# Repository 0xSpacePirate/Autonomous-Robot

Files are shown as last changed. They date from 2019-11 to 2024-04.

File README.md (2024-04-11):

## Self-balancing-Robot

This project focuses on building an autonomous single-wheeled self-balancing
humanoid robot made from scratch. This report presents the techniques used to
design the robot and using reinforcement learning (RL) and a PID Controller make it
self-balancing. In the project was also included a 3D Simulation.

One of the goals of the project was to make a brand new robot design and not copy
from the already created ones on the internet. The design was supposed to represent
the Robert Gordon University robot (see image below):

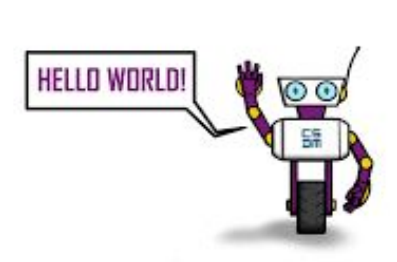
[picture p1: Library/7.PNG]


## Please refer to the pdf document for more detailed information! 
The pdf document can be found at: [Honours Project Report](https://github.com/SpacePirato/Autonomous-Robot/blob/master/Library/Honours%20Report%20-%20PETAR%20BONCHEV%20(1607262).pdf)

More info on the motivation & literature review can be found in the PDF document - chapters: 1-2;

-----------------------------------------------------------------------------------

The hardware that was used to control the robot:
1. Raspberry Pi 4 Model B
2. Gyroscope MPU-6050
3. Servo DXW90 (plastic) & Servo MG90S (metal) - both modified in 
                      order to be able to rotate with 360 degrees
4. Jumper cables
5. 6 AA 2900mAh batteries
6. Battery holder
7. UBEC 5V switch regulator

The first prototype can be seen below:

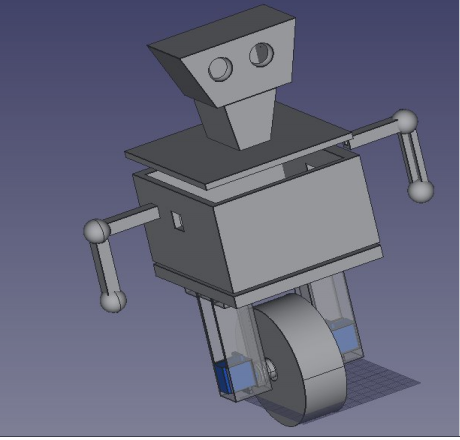
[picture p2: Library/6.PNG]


More info on the setup can be found in the PDF document - chapter: 3;

-----------------------------------------------------------------------------------

The design of the second prototype is more sophisticated and showed better results, 
however the legs had to be extended due to the reason that the robot was falling to quickly.

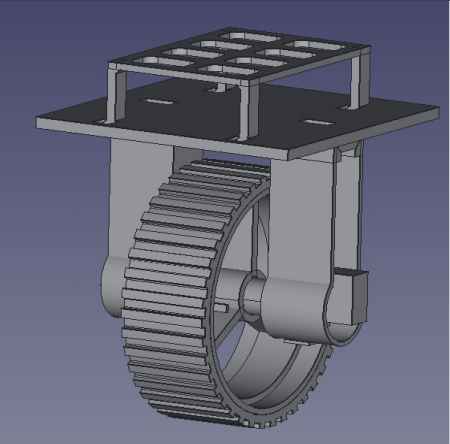
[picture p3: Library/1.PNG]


**The project was not finished**. Partially working self balacing robot using only a PID controller.
Examples can be seen below which represent the results from the first prototype:

-----------------------------------------------------------------------------------

The results from the two prototypes show that with the many improvements implemented, 
the robot manages to self balance itself better and better but not fully.

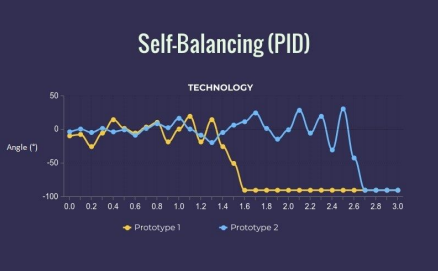
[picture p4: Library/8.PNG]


More detailed info on the results can be found in the PDF document - chapter 8;

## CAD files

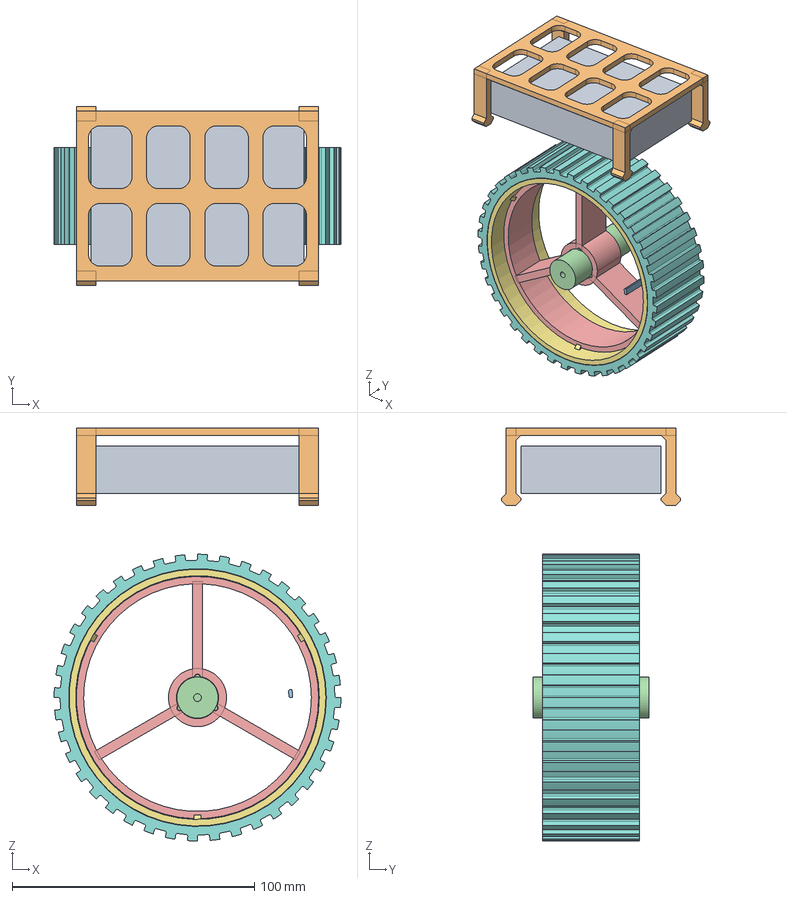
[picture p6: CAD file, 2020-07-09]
RobotAutoCAD/SecondPrototypeFinal.FCStd
118.4 x 74.0 x 170.5 mm
RPi
battery platform001
thread cut rounded for bigger tyre
axis with servo disc clicks
bigger hub (+2cm)
bigger hub install click
bigger rim (+2cm) with hub install clicks
bigger tyre with thread (+2cm)

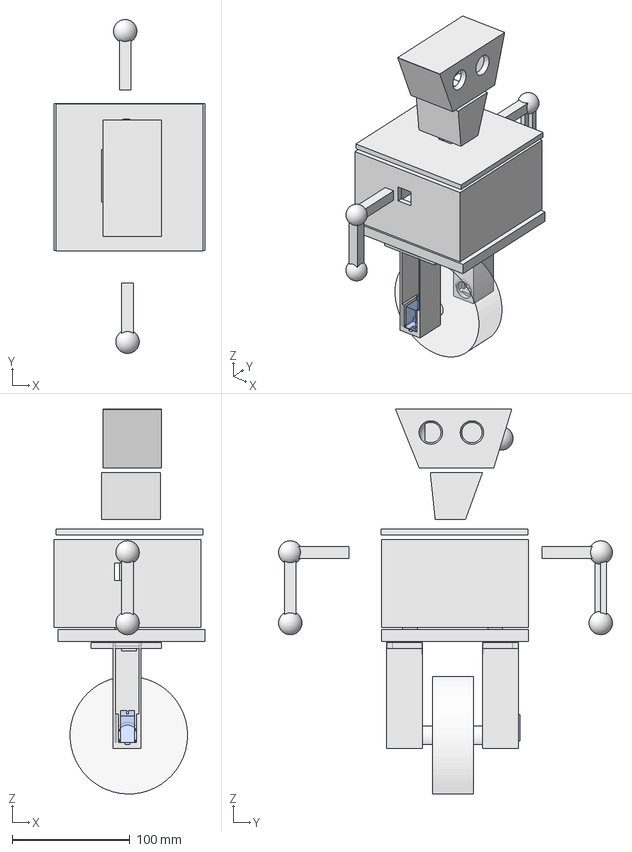
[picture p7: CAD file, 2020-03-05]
RobotAutoCAD/Robot (Prototype 1) FINAL.FCStd
128.3 x 283.9 x 327.4 mm
Head007
BaseTop002
BaseCover003
RightHand002
Base003
LeftHand002
Servo-sg90-final002
Servo-sg90-final002 (Mirror #2)
Wheel
Neck
Cut010 (Mirror #6)

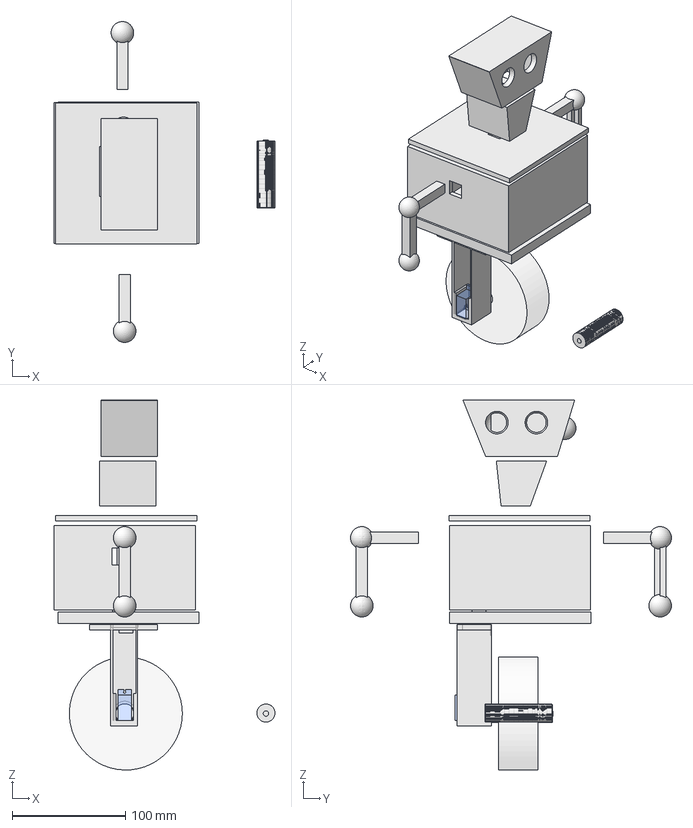
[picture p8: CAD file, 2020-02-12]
RobotAutoCAD/Robot( Prototype 1) Fixed Flaws.FCStd
195.5 x 283.9 x 327.4 mm
Head007
BaseTop002
BaseCover003
RightHand002
Base003
LeftHand002
Servo-sg90-final002
Wheel
WheelRod
Neck
RightLeg

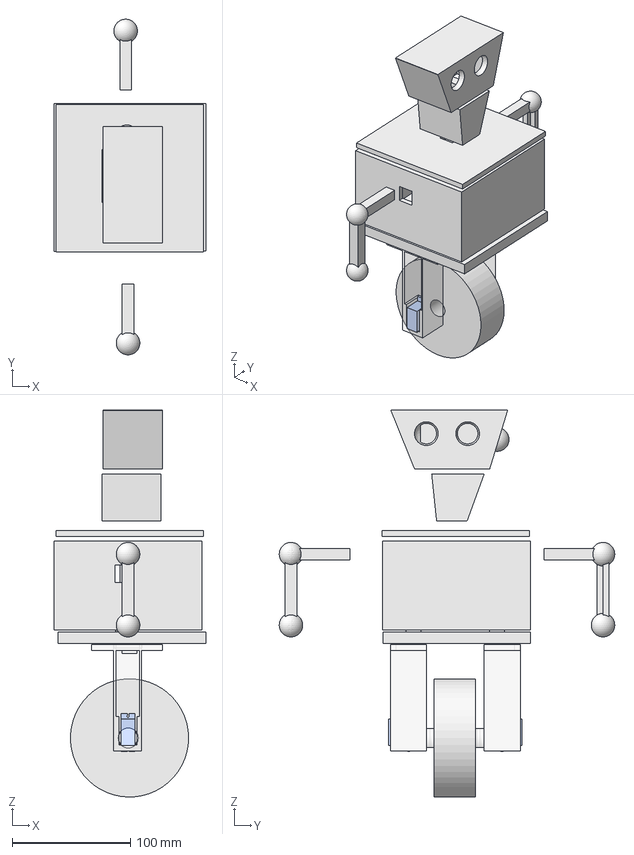
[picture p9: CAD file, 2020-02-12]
RobotAutoCAD/Robot( Initial final Prototype).FCStd
128.3 x 283.9 x 327.4 mm
Head007
BaseTop002
BaseCover003
RightHand002
Base003
LeftHand002
Servo-sg90-final002
Servo-sg90-final002 (Mirror #2)
Rod005
Cut008 (Mirror #4)

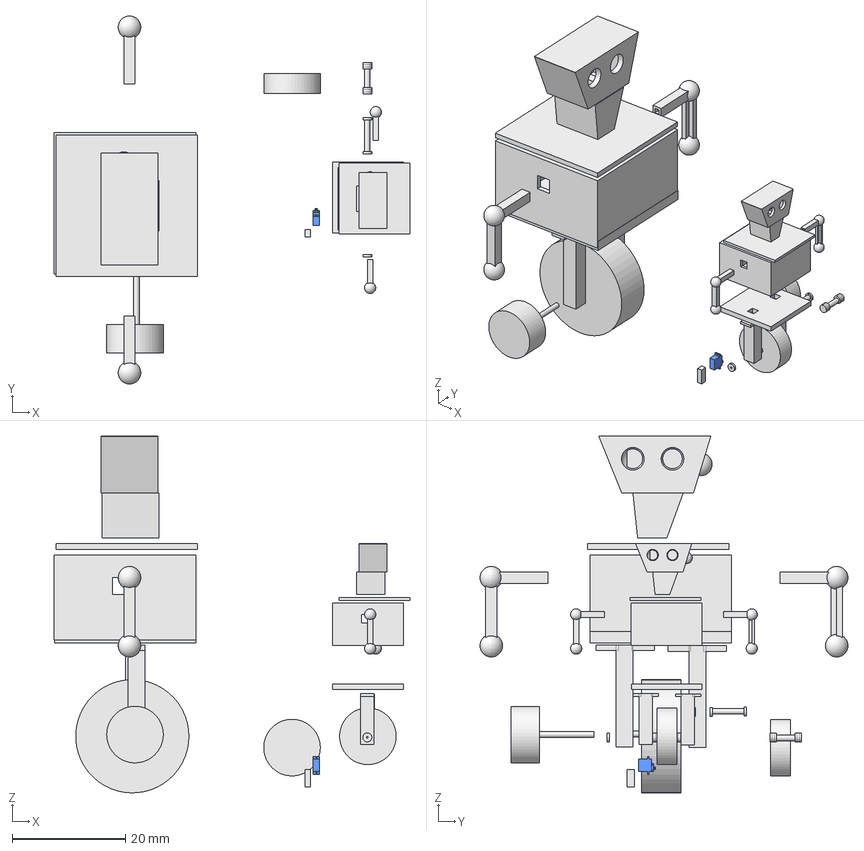
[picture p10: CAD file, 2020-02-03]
RobotAutoCAD/Robot.FCStd
62.8 x 65.0 x 63.0 mm
Base001
Wheel001
Rod
Neck
Head003
BaseCover001
BaseTop
RightHand
LeftHand
Head006
Neck001
BaseTop001
BaseCover002
Base002
LeftLeg009
RightLeg
RightHand001
LeftHand001
Rod002
Wheel003
Scale

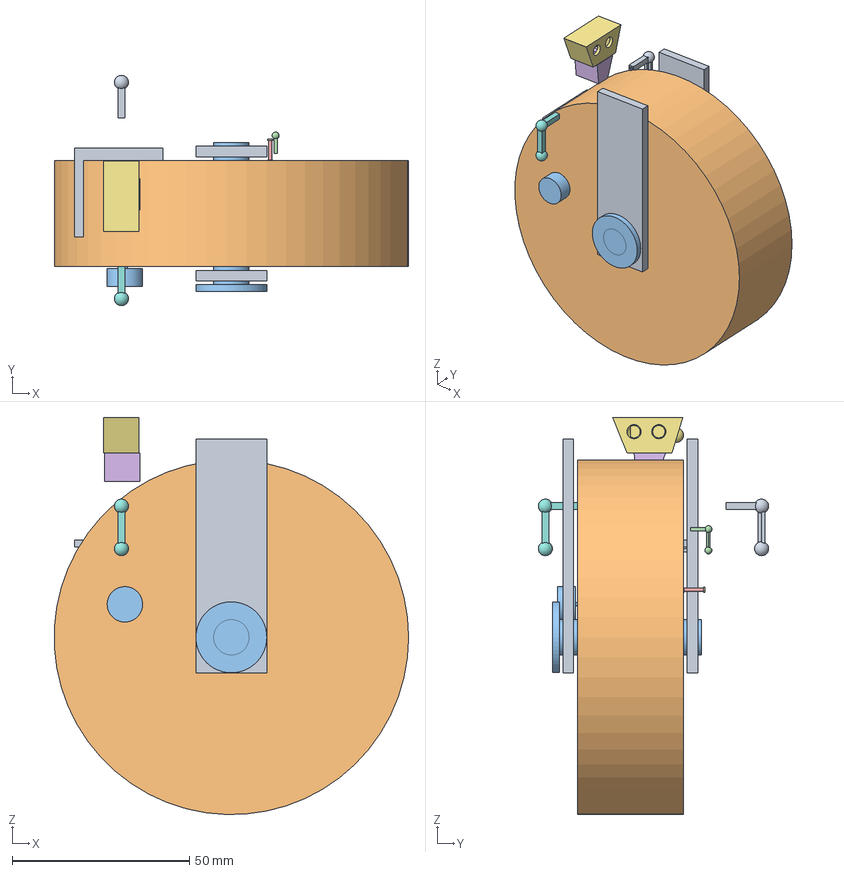
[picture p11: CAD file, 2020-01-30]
RobotAutoCAD/Robot (Kit).FCStd
99.9 x 65.0 x 112.0 mm
Base001
Wheel001
Rod
Neck
Head003
RightHand
LeftHand
Head006
Neck001
BaseTop001
BaseCover002
Base002
Wheel002
LeftLeg009
RightLeg
RightHand001
LeftHand001
Rod002
wheel support with holes
wheel with hole
axis with servo disc

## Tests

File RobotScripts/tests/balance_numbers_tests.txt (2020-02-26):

=====================================================================================================================
				 	  Gyroscope

Vertical
x = > 5.82 + 6.06 + 5.95 + 5.53 + 5.52 + 5.77 + 5.67 + 5.45 + 5.67 + 3.47 + 6.11 + 6.05 + 5.64 + 6.04 + 6.83 = 85.58
y = > 5.8 + 9.35 + 8.64 + 6.58 + 6.2 + 6.63 + 6.79 + 7.11 + 6.89 + 6.95 + 9.08 + 7.82 + 6.04 + 5.43 + 6.47 =‬ 105.78
Average: x = 5.7, y = 7.052
--------------------------------------------------------------------------------------------------------------
Left 
x = > 6.36 + 4.6 + 6.31 + 6.74 + 7.73 + 6.37 + 5.52 + 5.97 + 6.26 + 5.61 + 6.85 + 5.55 + 5.87 + 5.92 + 5.7 =‬ 91.36
y = > 4.91 + 5.65 + 9.43 + 7.05 + 5.56 + 4.5 + 5.89 + 6.15 + 6.1 + 5.11 + 4.6 + 6.35 + 5.24 + 5.97 + 6.17 =‬ 88.68
Average: x = 6.09, y = 5.912  
--------------------------------------------------------------------------------------------------------------
Right
x = > 5.54 + 5.76 + 4.49 + 5.05 + 5.95 + 4.58 + 6.8 + 5.81 + 5.45 + 5.94 + 4.24 + 4.31 + 6.85 + 5.65 + 4.26 = 80.68
y = > 5.36 + 6.1 + 5.11 + 5.67 + 5.51 + 5.09 + 7.94 + 7.19 + 7.15 + 4.25 + 5.78 + 6.79 + 4.96 + 6.21 + 6.08 =‬ 89.19
Average: x = 5.378, y = 5.946 
=====================================================================================================================
					Accelerometer

Vectical
x = > 0 - 0.14 - 0.2 - 0.19 - 0.19 - 0.2 - 0.22 - 0.04 - 0.14 - 0.17 - 0.21 - 0.17 - 0.19 - 0.2 - 0.16 - 0.18 = -2.6
y = > 0 + 0.02 + 0.02 + 0.06 + 0.05 + 0.05 + 0.04 + 0.05 + 0.06 + 0.07 + 0.07 + 0.07 + 0.09 + 0.05 + 0.06 = 0.76
z = > 1.08 + 1.08 + 1.07 + 1.07 + 1.08 + 1.06 + 1.1 + 1.07 + 1.07 + 1.07 + 1.06 + 1.06 + 1.07 + 1.06 + 1.07 = 16.07
Average: x = -0.173 , y = 0.05, z = 1.07
--------------------------------------------------------------------------------------------------------------
Left
x = > 0.61 - 0.62 - 0.65 - 0.65 - 0.63 - 0.66 - 0.63 - 0.63 - 0.61 - 0.63 - 0.64 - 0.65 - 0.67 - 0.69 - 0.67 = -9.64
y = > 0.11 + 0.1 + 0.13 + 0.13 + 0.14 + 0.15 + 0.12 + 0.11 + 0.12 + 0.12 + 0.09 + 0.12 + 0.13 + 0.15 + 0.11 = 1.83
z = > 0.83 + 0.84 + 0.83 + 0.84 + 0.83 + 0.82 + 0.84 + 0.84 + 0.85 + 0.86 + 0.84 + 0.82 + 0.81 + 0.79 + 0.8 = 12.44
Average: x = -0.64, y = 0.122‬, z = 0.829
--------------------------------------------------------------------------------------------------------------
Right
x = > 0.62 + 0.65 + 0.65 + 0.64 + 0.68 + 0.69 + 0.66 + 0.67 + 0.71 + 0.77 + 0.74 + 0.6 + 0.64 + 0.61 + 0.61 = 9.94
y = > 0.04 + 0.05 + 0.03 + 0.04 + 0.04 + 0.03 + 0.05 + 0.02 + 0.04 + 0.06 + 0.04 + 0.03 + 0.01 + 0.06 + 0.06 = 0.6
z = > 0.88 + 0.85 + 0.88 + 0.87 + 0.83 + 0.85 + 0.85 + 0.83 + 0.8 + 0.75 + 0.79 + 0.89 + 0.87 + 0.89 + 0.89 = 12.72
Average: x = 0.66, y = 0.04‬, z = 0.848
=====================================================================================================================

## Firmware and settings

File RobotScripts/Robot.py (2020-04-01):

import RPi.GPIO as GPIO
import time
from LeftServo import LeftServo
# from RightServo import RightServo
import RightServo as rightMotor
from threading import Thread
# import GyroReader as gyroScope
from GyroFilter import GyroFilter
from PIDBalancer import PIDBalancer
from PIDController import PIDController
from threading import Timer


# from simple_pid import PID


class Robot:
    print("Launch Configuration initiated")

    # DutyCycle = 1/18 * (DesiredAngle) + 2 (or + 2.5 -> check)

    def __init__(self):
        self.pid_balancer = PIDBalancer(37.0, 0.0, 0.0)
        self.gyroFilter = self.pid_balancer.get_gyro_filter()
        (self.gyro_scaled_x, self.gyro_scaled_y, self.gyro_scaled_z,
         self.accel_scaled_x, self.accel_scaled_y, self.accel_scaled_z) = self.gyroFilter.get_gyro_and_accel()
        # self.rightMotor = RightServo()
        self.leftMotor = LeftServo()

    def start_motors(self):
        # leftMotor.start()
        # self.rightMotor.start()
        rightMotor.start()
        print("Motors started")

    def stop_motors(self):
        # leftMotor.stop()
        # self.rightMotor.stop()
        rightMotor.stop()
        GPIO.cleanup()
        print("Motors stopped")

    def move_left(self):
        self.start_motors()
        left = 7.5  # move towards 90 degrees
        # self.rightMotor.stop()
        rightMotor.stop()
        self.leftMotor.move(left)

    def move_right(self):
        self.start_motors()
        right = 7.5  # move towards 90 degrees
        self.leftMotor.stop()
        # rightMotor.move(right)
        # self.rightMotor.move(right)
        rightMotor.move(right)

    def move_forward(self):
        self.start_motors()
        # forward = 5.5  # pid_value  # emphasizes that the pid value is being used
        # self.leftMotor.move(forward)
        # self.rightMotor.move(forward)

    def move_backwards(self):
        self.start_motors()
        # backwards = 12  # pid_value  # emphasizes that the pid value is being used
        # self.leftMotor.move(backwards)
        # self.rightMotor.move(backwards)

    def move_back(self):
        self.start_motors()
        back = 12.5
        # self.rightMotor.stop()
        rightMotor.stop()
        self.leftMotor.move(back)

    def set_angle(self, angle):
        duty = (1 / 36) * angle + 2
        return duty

    def balance(self):
        # gyroScope.print_all_data()
        print("\n\n------------ PID + Filter Below ---------------\n\n")
        # gyroFilter.print_all()
        # self.start_motors()

        try:
            while True:
                print("\n= = = = = = = = = = = = = = = = = =\n")
                # self.gyroFilter.print_all()
                self.pid_balancer.update_pid_error()
                pid_value = self.pid_balancer.get_pid_value()
                print("PID value = " + str(pid_value()))
                self.stabilize(pid_value())
                # self.move_forward()
                # self.gyroFilter.print_all()
                time.sleep(0.1)
                # self.stop_motors()
        except KeyboardInterrupt:
            print("Interrupted. End of stabilizing")

        # self.gyroFilter.print_all()
        # pid_value = self.pid_balancer.get_pid_value()
        # self.pid_balancer.update_pid_error()
        # self.move_forward()
        # # self.stabilize(pid_value())
        # self.gyroFilter.print_all()
        # (x, y) = self.gyroFilter.calc_xy_values()
        # print("X and Y ->  " + str(x) + " : " + str(y))

    def stabilize(self, pid_value):
        # DutyCycle = PulseWidth/Period, therefore
        # DutyCycle = PulseWidth/(1/frequency) = PulseWidth * frequency
        # DutyCycle = PulseWidth*frequency = .001*50=.05= 5%
        # pid = pid_value / 20  # Interpolate the number so it's compatible with the PWM signal
        # self.rightMotor.move(pid)
        # self.median_pid_filter.insert(0, pid)
        # self.median_pid_filter.pop()
        # average_pid = float(sum(self.median_pid_filter) / len(self.median_pid_filter))
        # print("PID AVG " + str(self.median_pid_filter[0]) + " | " + str(self.median_pid_filter[1]) + " | "
        #       + str(self.median_pid_filter[2]) + " | " + str(self.median_pid_filter[3]) + " | "
        #       + str(self.median_pid_filter[4]) + " = " + str(average_pid))
        # exponential_value = pow(2, pid)  # / 10  # test
        # rightMotor.move(pid)
        rightMotor.move(pid_value)
        # if pid_value > 0:
        #     self.move_forward()
        # else:
        #     self.move_backwards()
        # self.stop_motors()

# stop_motors()

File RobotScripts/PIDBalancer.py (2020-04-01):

import smbus
import math
import time
# import simple_pid
from GyroFilter import GyroFilter
from PIDController import PIDController
from MyDataReader import MyDataReader


# For more information refer to tests/balance_numbers_tests.txt
# Gyroscope Average Values;
# Vertical: x = 5.7, y = 7.052; Steady
# Left: x = 6.09, y = 5.946
# Right: x = 5.378, y = 5.946
# ====================
# Accelerometer Average Values
# Vertical: x = -0.173, y = 0.05, z = 1.07; Steady
# Left: x = -0.64, y = 0.122, z = 0.829
# Right: x = 0.66, y = 0.04, z = 0.848

class PIDBalancer:

    def __init__(self, kp, ki, kd):
        self.kp = kp
        self.ki = ki
        self.kd = kd

        self.gyro_vertical_center_x = 5.7
        self.gyro_vertical_center_y = 7.052

        self.median_filter = [0.0, 0.0, 0.0, 0.0, 0.0]
        gyro_scale = 131.0
        accel_scale = 16384.0
        RAD_TO_DEG = 57.29578
        M_PI = 3.14159265358979323846
        now = time.time()
        K = 0.98
        K1 = 1 - K

        time_diff = 0.01
        gyroAngleX = 0.0
        gyroAngleY = 0.0
        gyroAngleZ = 0.0
        accAngX = 0.0
        CFangleX = 0.0
        CFangleX1 = 0.0
        K = 0.98
        FIX = -12.89

        self.gyroFilter = GyroFilter()
        (self.gyro_scaled_x, self.gyro_scaled_y, self.gyro_scaled_z, self.accel_scaled_x, self.accel_scaled_y,
         self.accel_scaled_z) = self.gyroFilter.read_all()
        (self.accel_vertical_center_x, self.accel_vertical_center_y,
         self.accel_vertical_center_z) = self.gyroFilter.get_accel_center_xyz()
        pid_set_point = 0.00
        self.pid = PIDController(kp, ki, kd, pid_set_point)

        self.DataReaderMain = MyDataReader()
        self.data_reader = self.DataReaderMain.get_xyx()

        # The angle of the Gyroscope
        gyroAngleX += self.gyro_scaled_x * time_diff
        gyroAngleY += self.gyro_scaled_y * time_diff
        gyroAngleZ += self.gyro_scaled_z * time_diff

        accAngX = (math.atan2(self.accel_scaled_x, self.accel_scaled_y) + M_PI) * RAD_TO_DEG
        # math.atan2 numeric value between -PI and PI representing the angle theta of an (x, y) point.
        CFangleX = K * (CFangleX + self.gyro_scaled_x * time_diff) + (1 - K) * accAngX

        accAngX1 = self.get_x_rotation(self.accel_scaled_x, self.accel_scaled_y, self.gyro_scaled_z)
        # accAngX1 = get_x_rotation(accel_scaled_x, accel_scaled_y, gyro_scaled_x) or this one - test?

        CFangleX1 = (K * (CFangleX1 + self.gyro_scaled_x * time_diff) + (1 - K) * accAngX1)

    def dist(self, a, b):
        return math.sqrt((a * a) + (b * b))

    def get_current_data(self):
        self.data_reader = self.DataReaderMain.get_xyx()  # reassign, might use it for sth else
        return self.data_reader

    def get_y_rotation(self, x, y, z):
        radians = math.atan2(x, self.dist(y, z))
        return -math.degrees(radians)

    def get_x_rotation(self, x, y, z):
        radians = math.atan2(y, self.dist(x, z))
        return math.degrees(radians)

    def update_pid_error(self):
        average_accel_scaled_x = self.output_filter()
        # pid_error = self.accel_vertical_center_x - average_accel_scaled_x
        pid_error = average_accel_scaled_x
        # X, Y = self.gyroFilter.calc_xy_values()
        # print("X using X Y Z: " + str(X))
        # print("center: " + str(self.accel_vertical_center_x) + " current(AVG): " + str(
        #         #     average_accel_scaled_x) + " = " + str(pid_error))
        # print("center: " + str(self.accel_vertical_center_x) + " current(AVG): " + str(
        #      average_accel_scaled_x) + " = " + str(pid_error))
        self.pid.update_pid(pid_error)

    def get_pid_value(self):
        # print("Current XYZ: " + str(self.accel_scaled_x) + " | " + str(self.accel_scaled_y) + " | " + str(
        #    self.accel_scaled_z))
        return self.pid.get_pid

    def get_gyro_filter(self):
        return self.gyroFilter

    def output_filter(self):
        # (self.gyro_scaled_x, self.gyro_scaled_y, self.gyro_scaled_z, self.accel_scaled_x, self.accel_scaled_y,
        #  self.accel_scaled_z) = self.gyroFilter.read_all()
        self.data_reader = self.DataReaderMain.get_xyx()
        x_value = self.data_reader[0]

        if self.data_reader[2] <= 0:  # if accel x is >= 0, the robot falls forward
            x_value = -x_value

        self.median_filter.insert(0, x_value)  # self.data_reader[0] stands for value of X;
        self.median_filter.pop()
        average_accel_scaled_x = float(sum(self.median_filter) / len(self.median_filter))
        print("ACCEL AVG " + str(self.median_filter[0]) + " | " + str(self.median_filter[1]) + " | "
              + str(self.median_filter[2]) + " | " + str(self.median_filter[3]) + " | "
              + str(self.median_filter[4]) + " = " + str(average_accel_scaled_x))
        return average_accel_scaled_x

    # print(
    #    "{0:.2f} {1:.2f} {2:.2f} {3:.2f} | {4:.2f} {5:.2f} | {}".format(gyroAngleX, gyroAngleY, accAngX, CFangleX,
    #                                                                         accAngX1, CFangleX1, pid))

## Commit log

2020-01-22 Working servos, including them being able to turn left, right, and back
2020-01-23 GY-521 working code. Added the PID code, yet to be adjusted
2020-01-24 PID and gyroFilter bug fix - both working now
    [GyroFilter.py, GyroReader.py, Robot.py]
2020-01-24 PID bug fix where it was not using the gyroFilter data
    [LeftServo.py, PIDBalancer.py, RightServo.py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]
2020-01-27 AutoCAD Robot body uploaded
    [Robot.FCStd]
2020-01-28 Finished initial Robot design
    [Robot.FCStd]
2020-01-28 PID bug fixes
2020-01-29 Addinationa details to the robot, plus a smaller prototype of it
    [Robot.FCStd]
2020-01-30 Wheel rod design fixes
    [Robot (Kit).FCStd, Robot(edited).FCStd, Robot.FCStd]
2020-01-30 did PWM tests and added comments
2020-01-31 did additional PWD tests
    [Robot.FCStd]
2020-02-03 Updated design of the robot
    [Robot.FCStd]
2020-02-03 Changed design of the legs
2020-02-04 Final initial robot 3D prototype
2020-02-05 Update the scale of the AutoCAD robot prototype
    [Robot( Initial final Prototype).FCStd]
2020-02-05 new PID Controller, updated PIDBalancer and Robot classes
2020-02-11 Robot Prototype one - design flaws->fixed, except leg rod hole and leg top
    [Robot( Initial final Prototype).FCStd]
2020-02-12 Robot mechanical prototype 1 - design flaws fixed
    [Robot( Initial final Prototype).FCStd, Robot( Prototype 1) Fixed Flaws.FCStd]
2020-02-12 Prototype 1 - secondary flaws found and fixed - legs sides not flat on the very top, a micro hole between the servo holder and the leg
    [Robot( Prototype 1) Fixed Flaws.FCStd]
2020-02-12 Robot prototype 1 - fixed the Rod axis alignment
    [Robot (Prototype 1) FINAL.FCStd, Robot( Prototype 1) Fixed Flaws.FCStd]
2020-02-19 refactor + wheel tests bugs fixed(issue was caused by motors.stop())
    [GyroFilter.py, Robot.py]
2020-02-26 added gyroscope and accelerometer test values, file, comment
2020-02-27 pid updates, refactor, additional methods
2020-02-29 Mapped PID output - done, big fixes. refactor, tests. Has to be fixed: for the last tests the output from PID is zero
    [LeftServo.py, PIDController.py, RightServo.py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]
2020-02-29 PID output being zero bug fixed
    [Robot.py]
2020-03-01 gyroscope reading bug fixed
    [GyroReader.py, PIDBalancer.py, PIDController.py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]
2020-03-01 PID tune, almost balancing | bug fixes
    [GyroFilter.py, PIDBalancer.py, RightServo.py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]
2020-03-02 Small changes to PID tune
2020-03-03 added output filter, move bug fixed, PID tune, getting closer!
    [GyroFilter.py, PIDBalancer.py, RightServo.py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]
2020-03-05 robot design update - added place for the servo motor on the robot's legs
    [Robot (Prototype 1) FINAL.FCStd]
2020-03-07 3D Simulation, fixed PID balance bug. Added left and right turns.
2020-03-07 added another window filter to the Hardware Robot
2020-03-10 Robot Hardware PID tune updates | RL additional comments
2020-03-13 fixed the output filter
    [PIDBalancer.py, RightServo.py]
2020-03-13 added exponential function (needs testing, removed the thread sleep since the robot balances better without it
2020-03-14 hardware updates (doesnt work with prototype 3)
2020-04-01 switched from software PWM to hardware PWM
